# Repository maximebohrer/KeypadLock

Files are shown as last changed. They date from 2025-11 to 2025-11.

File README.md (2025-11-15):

Keypad Door Lock
================

This project turns a conventional door with key into a electronic lock with numerical keypad and password access.

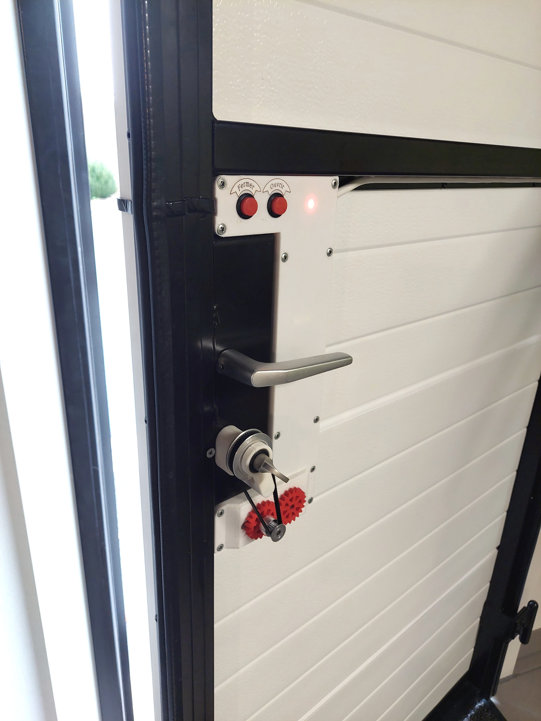
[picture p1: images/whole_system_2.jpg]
Whole system


Most keypad locks that can be bought have all the electronics in the keypad in the exterior of the door, only triggering the door opening by sending a signal to a wire. This means they can be bypassed by dismantling the keypad and touching wires manually.

This version only exposes a passive matrix keypad to the exterior, with all the logic used to interpret the keypresses and opening the door in the inside. There is no way to open the door without knowing the combination, even if the keypad is dismanteled. Two buttons in the inside are used to open or close the door without having to enter the conbination.

Keypad

The system is continuously powered by a 12V supply, which is required for the motor. A LM7805 voltage regulator is used to create 5V for the microcontroller.

The microcontroller used is a Atmel ATmega328P which is the same used in the Adruino Uno and Nano. It is programmed using the Arduino environment.

I needed a motor with the following caracteristics:
- High torque and low speed in a small form factor without the need of a complicated reductor
- Can be rotated by hand when not powered, so that a key can still be used to open the door
- Easily controlled by the microcontroller
The stepper motor is an interesing choice for these reasons, even if we don't necessarily need the precision it offers. It is linked to the key using GT2 pulley and belt with a 3:1 reduction ratio, to get a bit more torque from the motor. The motor is controller by the A4988 IC, to which the microcontroller only has to give step and direction commands.

Motor, pulleys and belt

The system is aware of the position of the key (the rotation angle) with the help of a potentiometer. It is a 10 turn potentiometer (the key has to be able to do multiple full rotations in the door) that is effectively used as a obsolute encoder. It is connected to the key via a 1:1 ratio.

Motor and potentiometer

One LED and buzzer are additionaly used to give feedback to the user.

The PCB was designed on EasyEDA and printed by JLCPCB.

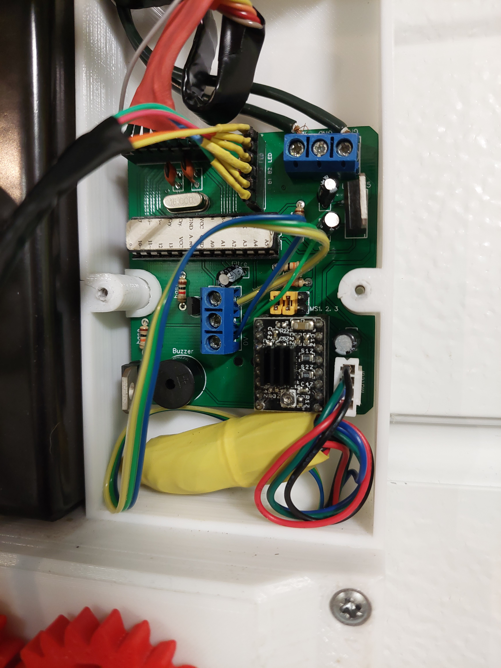
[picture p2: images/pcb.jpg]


The case was designed to fit the door and was 3D-printed. Is has a place for the power supply, PCB, motor and potentiometer, and space for routing cables. It includes a mecanism to tension the GT2 belt by moving the motor+potentiometer block.

Material list
-------------

- ATmega328P with crystal and capacitors
- Nema 17 stepper motor
- A4988 controller
- 12V 5A power supply
- GT2 20-tooth pulley
- GT2 60-tooth pulley
- GT2 280 mm belt
- 8 mm shaft
- 8 mm ball bearing
- 10-turn potentiometer
- 12V 2A power supply
- 12-key keypad
- Red LED
- 2 buttons
- 3D-printed enclosure
- 3D-printed gears
- Custom made PCB
- Wires, screws, etc.

User manual
-----------

```
┌── Log In and Open Door ─────────────────────────────────────────┐
│   ‾‾‾‾‾‾‾‾‾‾‾‾‾‾‾‾‾‾‾‾                                          │
│ You must first unlock the system before you can use any of      │
│ the following commands (except close door)                      │
│  *  0 0 1 2 3 4 5 0 0  #                                        │
│ └┬┘└──────────────┬──┘└─┘                                       │
│  └ start system   └ type the password                           │
│                                                                 │
├── Open Door ───────────────────┬── Close Door ──────────────────┤
│   ‾‾‾‾‾‾‾‾‾                    │   ‾‾‾‾‾‾‾‾‾‾                   │
│ To open the door, use the      │ To close the door, use the     │
│ following command              │ following command              │
│  1  #                          │  0  #                          │
│ └─┘└─┘                         │ └─┘└─┘                         │
│                                │                                │
├── Change Password ─────────────┴────────────────────────────────┤
│   ‾‾‾‾‾‾‾‾‾‾‾‾‾‾‾                                               │
│ To set a new password                                           │
│  7 7 7 1  0 0 1 2 3 4 5 0 0  #                                  │
│ └───────┘└────────┬────────┘└─┘                                 │
│                   └ new password (4 - 12 characters)            │
│                                                                 │
├── Set Trajectory ───────────────────────────────────────────────┤
│   ‾‾‾‾‾‾‾‾‾‾‾‾‾‾                                                │
│ To reset the trajectory and set its first point                 │
│ Move the key to the first position (door fully closed)          │
│ and type the following command                                  │
│  7 7 7 2  #                                                     │
│ └───────┘└─┘                                                    │
│                                                                 │
│ To set the next points (at least 2 in total and up to 10)       │
│ Move the key to the next position and chose the speed at        │
│ which the motor will reach that point                           │
│  7 7 7 2  1 0 0 0  #                                            │
│ └───────┘└───┬───┘└─┘                                           │
│              └ speed to get there in Hz (30 - 10000)            │
│                                                                 │
│ Example with 4 points                                           │
│   7772            77723000          77721000          77723000  │
│     ├─────────────────┼─────────────────┼─────────────────┤     │
│     ↑    ←3000 Hz→    ↑    ←1000 Hz→    ↑    ←3000 Hz→    ↑     │
│ first point     intermediate      intermediate       last point │
│ (door fully         point             point         (door fully │
│   closed)                                              open)    │
│                                                                 │
├── Set Acceleration ─────────────────────────────────────────────┤
│   ‾‾‾‾‾‾‾‾‾‾‾‾‾‾‾‾                                              │
│ To set the rate at which the motor speeds up and slows down     │
│  7 7 7 3  1 0 0 0 0  #                                          │
│ └───────┘└────┬────┘└─┘                                         │
│               └ acceleration in Hz/s (500 - 60000)              │
│                                                                 │
├── Set Timeout ──────────────────────────────────────────────────┤
│   ‾‾‾‾‾‾‾‾‾‾‾                                                   │
│ If the motor can't turn the key and is blocked for this         │
│ amount of time, it will stop and signal the fault               │
│  7 7 7 4  1 0 0 0  #                                            │
│ └───────┘└───┬───┘└─┘                                           │
│              └ timeout value in ms (10 - 5000)                  │
│                                                                 │
├── Installation ─────────────────────────────────────────────────┤
│   ‾‾‾‾‾‾‾‾‾‾‾‾                                                  │
│ The motor must be wired such that it turns in the right         │
│ direction when the OPEN and CLOSE buttons are pressed.          │
│                                                                 │
│ The potentiometer must be wired such that its voltage is at     │
│ its lowest when the door is closed, and increases as the door   │
│ opens.                                                          │
│                                                                 │
└─────────────────────────────────────────────────────────────────┘
```

Programming
-----------

To program microcontrollers in the Arduino envorinment you can use the Arduino IDE, the Arduino extension in VS code, PlatformIO, etc. I used the Arduino IDE.

There are two options to flash a standalone microcontroller:
- The default option: the upload button in the Arduino IDE flashes the program via the serial port (RX and TX pins). This requires a special bootloader on the microcontroller, already preinstalled on Arduino boards, whose job is to listen to the serial port when the microcontroller starts: if something is available, it writes the new program to memory, if not, it justs starts the existing one. [More information](https://docs.arduino.cc/retired/hacking/hardware/building-an-arduino-on-a-breadboard/)
- Flashing using an AVR programmer: it's a chip that directly writes a program to the microcontroller by using its programming pins. To do that we use the "upload via programmer" option of the Arduino IDE. The appropriate programmer has to be chosen in the list. We can even use another Arduino board as a programmer by flashing the ArduinoISP program to it, connecting the correct pins to the microcontroller, and selecting the "Arduino as ISP" programmer in the list. In this case the Arduino bootloader is no longer needed. If we want to use the microcontroller in an Arduino board again, we must use the "burn bootloader" option. [More information](https://docs.arduino.cc/built-in-examples/arduino-isp/ArduinoToBreadboard/)

Electric schematic and PCB
--------------------------

The electric schematic and PCB were created using EasyEDA and printed by JLCPCB.

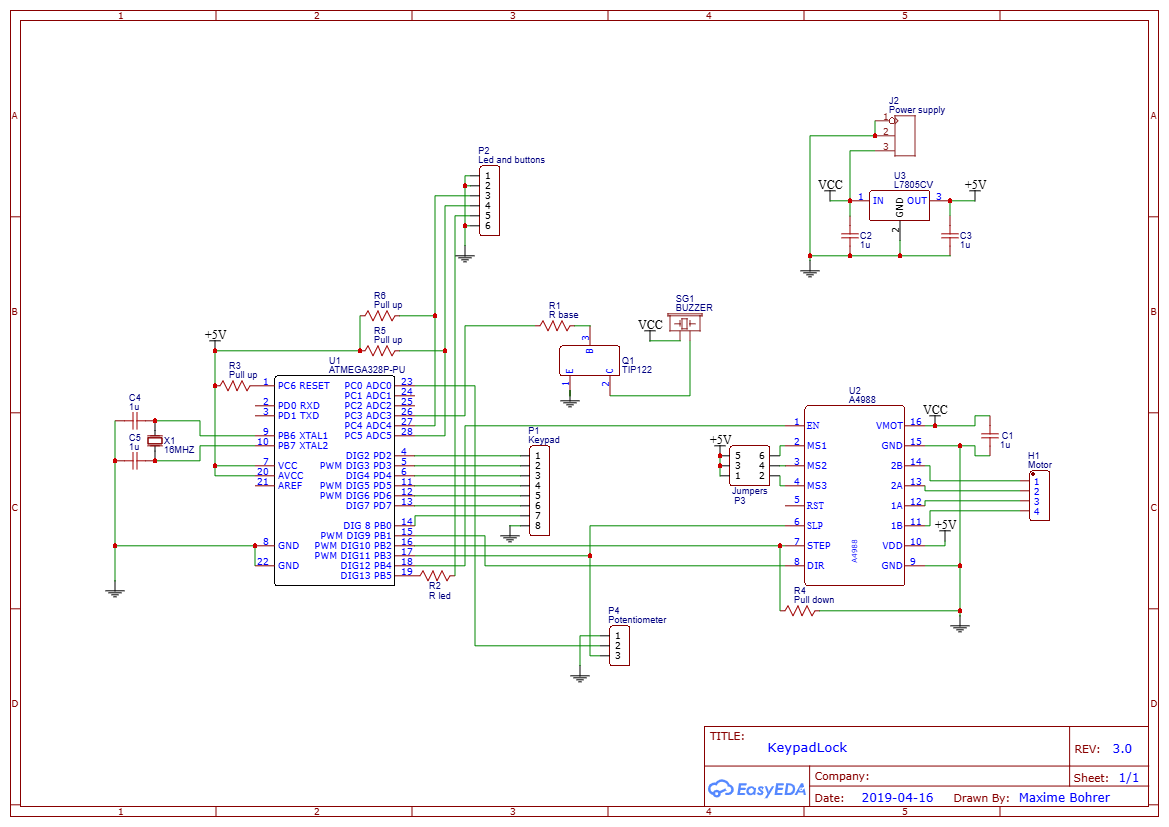
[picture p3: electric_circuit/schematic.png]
Electric schematic

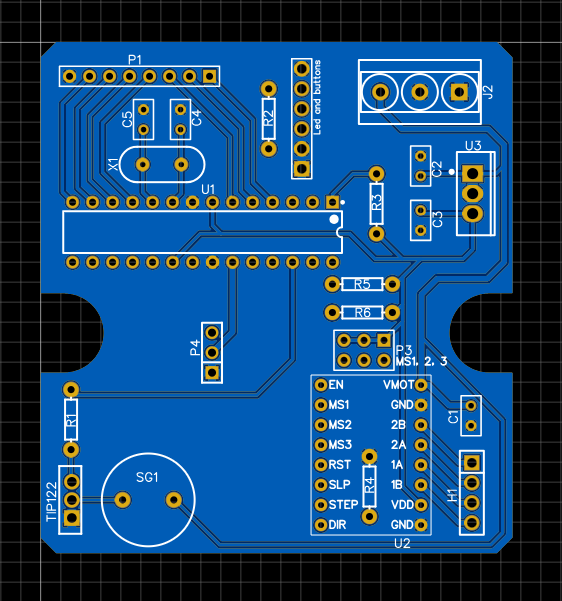
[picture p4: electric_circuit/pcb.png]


3D models
---------

The 3D models were created using Sketchup.

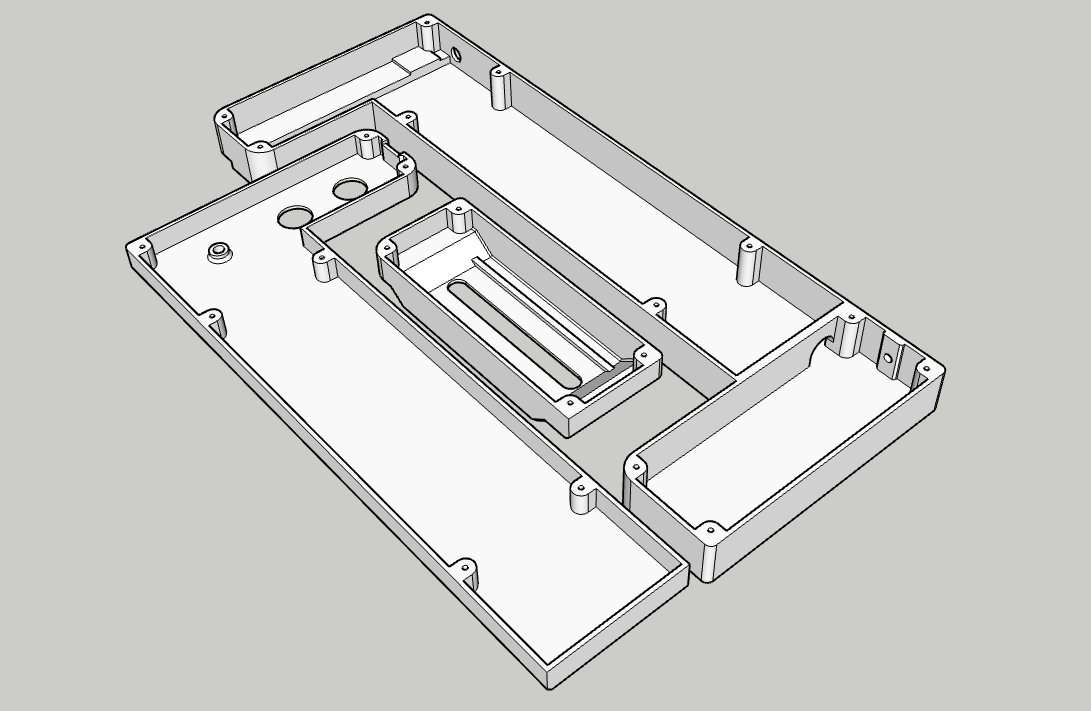
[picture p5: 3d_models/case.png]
Case 3D model


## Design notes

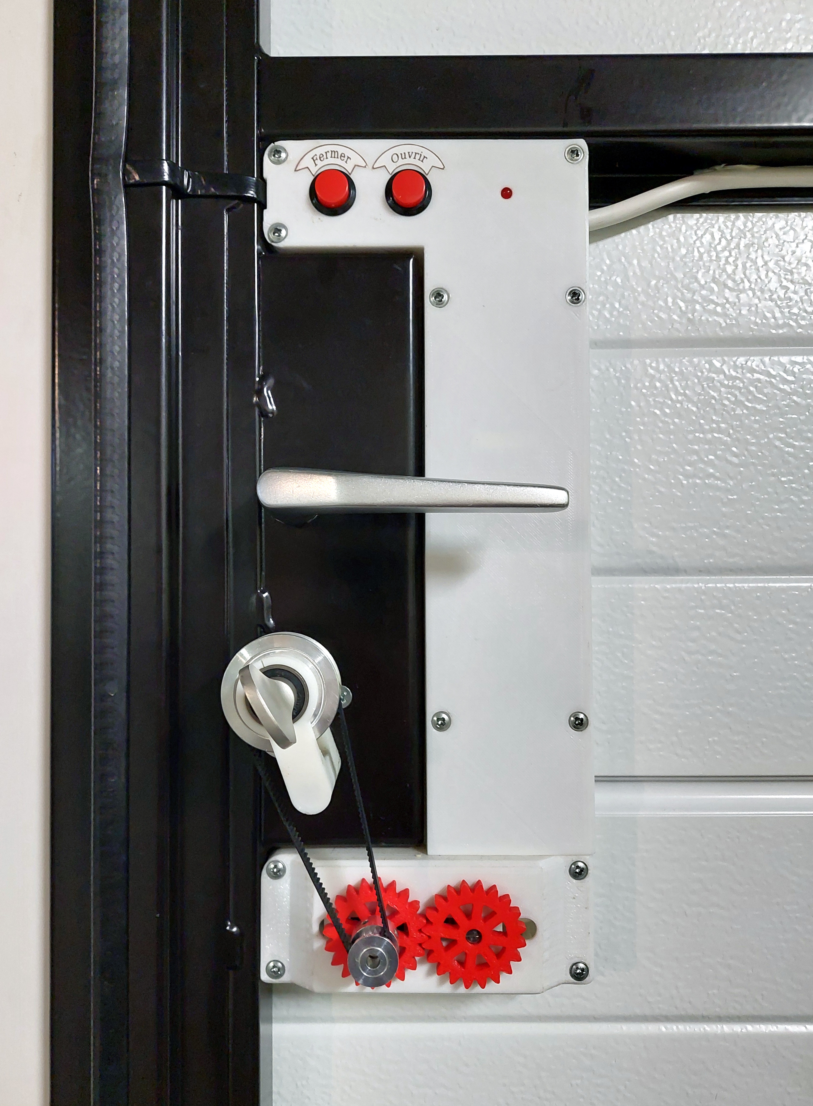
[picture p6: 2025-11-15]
images/whole_system_1.jpg

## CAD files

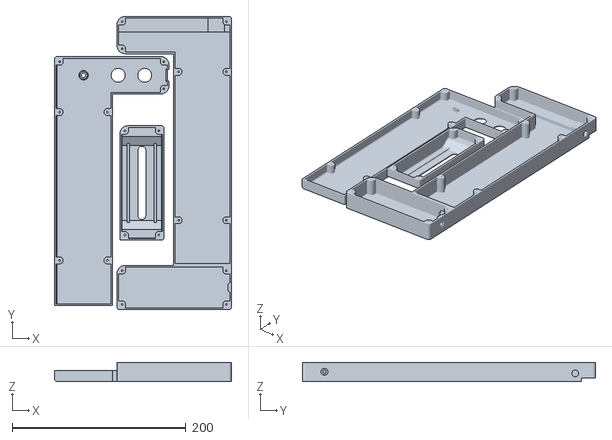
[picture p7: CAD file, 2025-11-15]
3d_models/case.stl
204.0 x 338.0 x 22.1

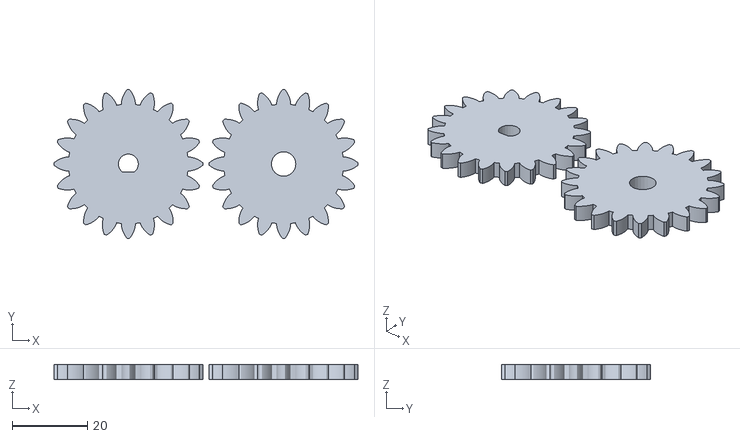
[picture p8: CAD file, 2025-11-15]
3d_models/gears.stl
80.8 x 39.6 x 4.00

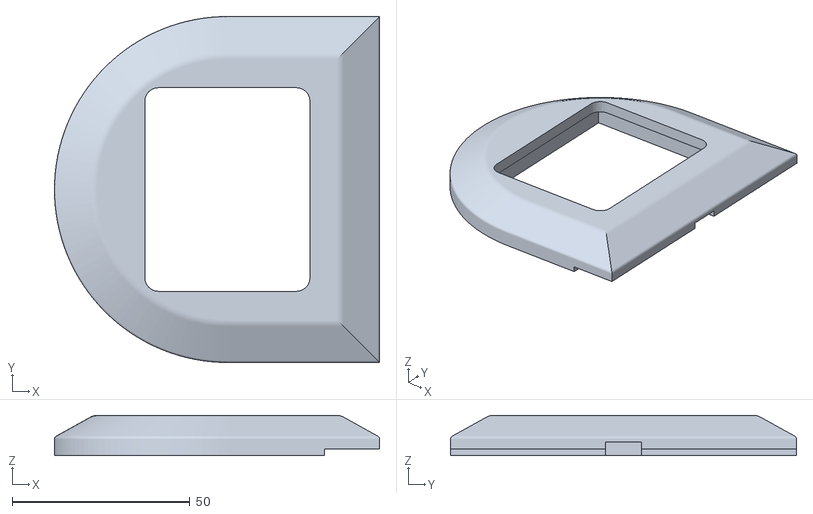
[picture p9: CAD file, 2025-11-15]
3d_models/keypad.stl
91.4 x 97.2 x 11.3

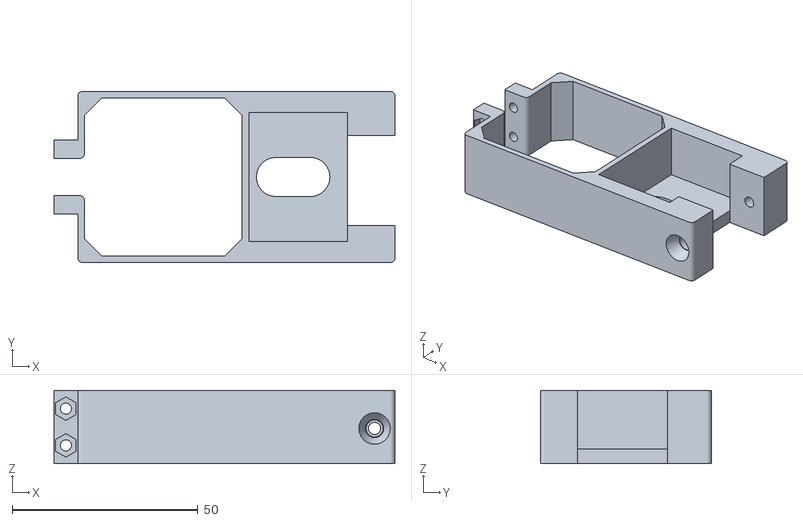
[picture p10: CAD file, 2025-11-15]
3d_models/motor_holder.stl
91.9 x 46.1 x 19.8

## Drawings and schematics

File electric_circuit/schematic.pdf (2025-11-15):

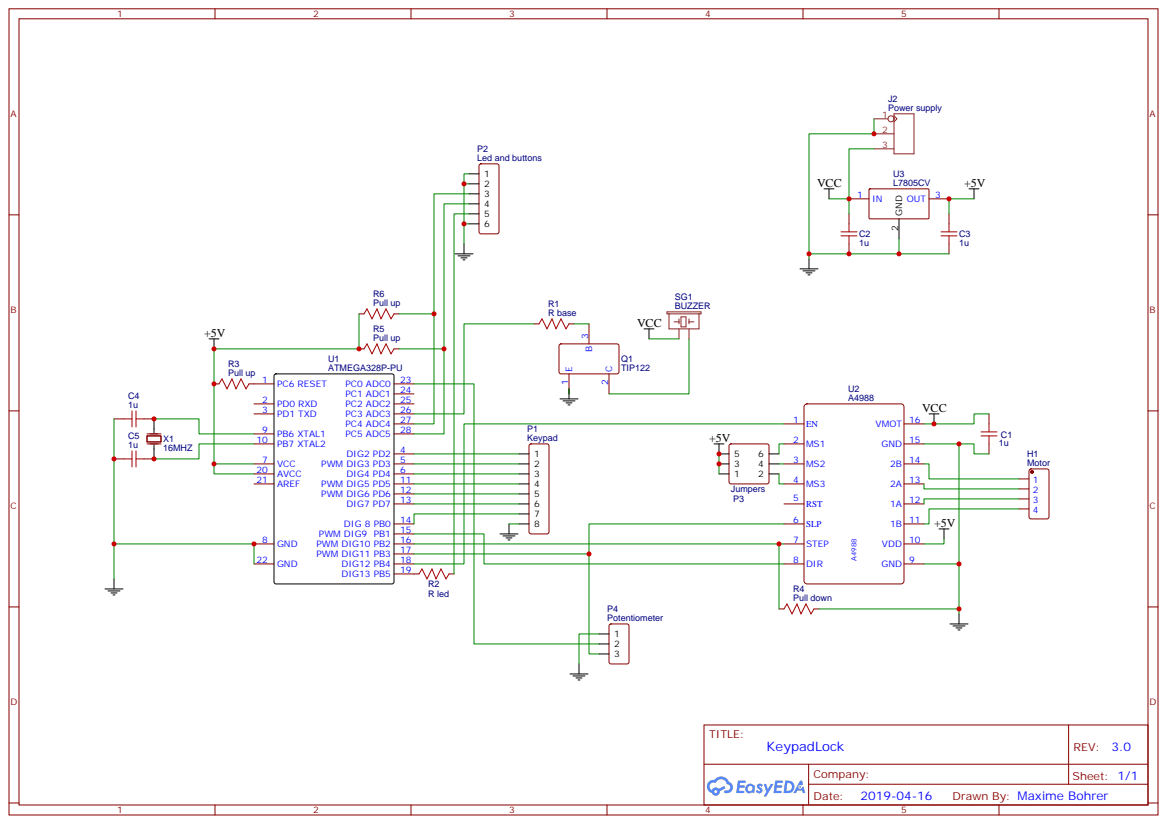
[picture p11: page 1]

Drawn By: Maxime Bohrer

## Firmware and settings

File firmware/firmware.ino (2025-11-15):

#include "SimpleKeypad.h"
#include "SimpleButton.h"
#include "Anim.h"
#include <EEPROM.h>

#define potPin A0       // Potentiometer input pin
#define stepPin 10      // A4988 step signal
#define dirPin 9        // A4988 direction signal
#define enablePin 12    // A4988 enable signal
#define sleepPin 11     // A4988 sleep signal
#define closeBtnPin A4  // Close button
#define openBtnPin A5   // Open button

#define SLEEP 0
#define AWAKE 1
#define UNLOCKED 2

#define TIME_BEFORE_SLEEP 30000

#define MOTOR_STATE_STOP 0
#define MOTOR_STATE_CLOSE 1
#define MOTOR_STATE_OPEN 2
#define MOTOR_STATE_WAIT_CLOSE 3
#define MOTOR_STATE_WAIT_OPEN 4

#define MOTOR_FREQ_ZERO 10
#define MOTOR_FREQ_MIN 30
#define MOTOR_FREQ_MAX 10000
#define MOTOR_FREQ_DEFAULT 1000

#define MOTOR_ACCEL_MIN 500
#define MOTOR_ACCEL_MAX 60000
#define MOTOR_ACCEL_DEFAULT 10000

#define MOTOR_TIMEOUT_MIN 10
#define MOTOR_TIMEOUT_MAX 5000
#define MOTOR_TIMEOUT_DEFAULT 1000

#define INPUT_BUFFER_SIZE 20

// Menu and settings
byte state = SLEEP;
unsigned long sleepTimer = 0;
struct settings {
	char password[INPUT_BUFFER_SIZE];
	int nbStops;
	int stops[10];
	unsigned int speeds[9];
	unsigned int accel;
	int timeout;
};
settings stngs;
bool trajectoryResetted = false;
char input[INPUT_BUFFER_SIZE] = "";
int inputPointer = 0;

// Motor
byte motorState = MOTOR_STATE_STOP;
int depart = 0;
unsigned long motorTimer = 0;
volatile bool stepPinState = 0;
volatile int motorFreq = MOTOR_FREQ_MIN;
volatile int motorFreqTarget = MOTOR_FREQ_MIN;
volatile int remainder = 0;
unsigned long timeoutTimer;
int currentSegment = 0;

// Buttons and keypad
const byte ROWS = 4;
const byte COLS = 3;
char keys[ROWS][COLS] = {
	{'1', '2', '3'},
	{'4', '5', '6'},
	{'7', '8', '9'},
	{'*', '0', '#'}
};
byte rowPins[ROWS] = {3, 8, 7, 5};
byte colPins[COLS] = {4, 2, 6};
SimpleKeypad clav((char*)keys, rowPins, colPins, ROWS, COLS);
SimpleButton closeBtn(closeBtnPin);   // Button on pin A4
SimpleButton openBtn(openBtnPin);     // Button on pin A5
SimpleButton starBtn(rowPins[3]);     // Button '*' of keypad. The star key is both a keypad key and a normal button, so that we can just check for this button in sleep mode instead of scanning the whole keypad.


void setup() {
	pinMode(stepPin, OUTPUT);
	pinMode(dirPin, OUTPUT);
	pinMode(enablePin, OUTPUT);
	pinMode(sleepPin, OUTPUT);
	pinMode(potPin, INPUT);
	pinMode(ledPin, OUTPUT);
	pinMode(buzzerPin, OUTPUT);

	digitalWrite(enablePin, HIGH);
	digitalWrite(sleepPin, LOW);
	digitalWrite(ledPin, HIGH);
	delay(500);
	digitalWrite(ledPin, LOW);
	pinMode(colPins[0], OUTPUT);    // on commance avec la touche * en mode bouton
	digitalWrite(colPins[0], LOW);  //

	// Timer 1 configuration
	TCCR1A = 0b00000000;
	TCCR1B = 0b00001000; // CTC mode (Clear Timer on Compare Match) with OCR1A as top. No clock source (timer stopped).
	TIMSK1 = 0b00000000; // All interrupts are disabled.
	TCNT1 = 0;           // Initializes the timer counter value to 0.

	loadSettings();
	resetCheckOnStartup();
}

void loop() {
	if (state != SLEEP) {
		// System is awake
		char key = clav.getKey();
		if (closeBtn.getState()) {
			// Close button
			if (motorState == MOTOR_STATE_STOP) {
				wakeUp();
				motorStart(MOTOR_STATE_CLOSE);
			} else {
				motorStop();
				beep(ALLUMAGE, false);
			}
		} else if (openBtn.getState()) {
			// Open button
			if (motorState == MOTOR_STATE_STOP) {
				wakeUp();
				motorStart(MOTOR_STATE_OPEN);
			} else {
				motorStop();
				beep(ALLUMAGE, false);
			}
		} else if (key) {
			// Keypad key
			wakeUp();
			if (key == '#') {
				handlePoundKey();
			} else if (key == '*') {
				handleStarKey();
			} else {
				inputAdd(key);
				beep(SHORT_BEEP, false);
			}
		}

		// Calling other loops
		if (motorState != MOTOR_STATE_STOP) {
			motorLoop();   // Motor loop
		} else {
			sleepLoop();   // Sleep management loop
		}
		animLoop();      // Animations loop
	} else {
		// System sleeping
		if (closeBtn.getState()) {
			// Close button
			wakeUp();
			motorStart(MOTOR_STATE_WAIT_CLOSE); // If the system is woken up by the open or close button, give it a bit of time before starting the motor
		} else if (openBtn.getState()) {
			// Open button
			wakeUp();
			motorStart(MOTOR_STATE_WAIT_OPEN);
		} else if (starBtn.getState()) {
			// Star button
			clav.ignoreNextKey('*'); // When the system wakes up, the scan of the keypad will resume, so we need to not register the star key since it's pushed down at this point.
			wakeUp();
			beep(ALLUMAGE, false);
		}
	}
}

void wakeUp() {
	if (state == SLEEP) {
		state = AWAKE;
		ledOn();
		digitalWrite(sleepPin, HIGH);
		digitalWrite(colPins[0], HIGH);
		pinMode(colPins[0], INPUT);
	}
	sleepTimer = millis();
}

void sleep() {
	state = SLEEP;
	digitalWrite(sleepPin, LOW);
	backgroundBlinkOff();
	ledOff();
	noBeep();
	inputReset();
	pinMode(colPins[0], OUTPUT);
	digitalWrite(colPins[0], LOW);
	starBtn.ignoreNextPress();
	trajectoryResetted = false;
}

void sleepLoop() {
	if (millis() - sleepTimer > TIME_BEFORE_SLEEP) {
		sleep();
	}
}

void inputAdd(char c) {
	if (inputPointer < INPUT_BUFFER_SIZE - 1) {
		input[inputPointer] = c;
		inputPointer++;
		input[inputPointer] = '\0'; // Null terminate string
	}
}

void inputReset() {
	inputPointer = 0;
	input[0] = '\0'; // Null terminate string
}

void handleStarKey() {
	if (input[0]) {
		inputReset();
		beep(ALLUMAGE, false);
	} else if (motorState != MOTOR_STATE_STOP) {
		motorStop();
		beep(ALLUMAGE, false);
	} else {
		sleep();
	}
}

void handlePoundKey() {
	if (!strncmp(input, stngs.password, INPUT_BUFFER_SIZE)) {
		state = UNLOCKED;
		motorStart(MOTOR_STATE_OPEN);
	} else if (state == UNLOCKED && !strncmp(input, "1", INPUT_BUFFER_SIZE) && motorState == MOTOR_STATE_STOP) {
		// open
		motorStart(MOTOR_STATE_OPEN);
	} else if (!strncmp(input, "0", INPUT_BUFFER_SIZE) && motorState == MOTOR_STATE_STOP) {
		// close
		motorStart(MOTOR_STATE_CLOSE);
	} else if (state == UNLOCKED && !strncmp(input, "7771", 4)) {
		// Password change
		int len = strnlen(input + 4, INPUT_BUFFER_SIZE - 4);
		if (len >= 4 && len <= 12 && strncmp(input + 4, "777", 3)) {
			strncpy(stngs.password, input + 4, INPUT_BUFFER_SIZE);
			saveSettings();
			beep(VALIDATION, false);
		} else {
			beep(SHORT_ERROR, true);
		}
	} else if (state == UNLOCKED && !strncmp(input, "7772", 4)) {
		// Key rotation trajectory / end stops
		if (!input[4]) {
			// Reset trajectory, save first point (door closed)
			trajectoryResetted = true;
			stngs.stops[0] = get_pos();
			stngs.nbStops = 1;
			saveSettings();
			beep(VALIDATION, false);
		} else {
			// Save next points with associated speeds in Hz (until door open)
			int pos = get_pos();
			long speed = strtol(input + 4, NULL, 10);                 // previous point
			if (trajectoryResetted && stngs.nbStops < 10 && pos > stngs.stops[stngs.nbStops - 1] + 1 && speed >= MOTOR_FREQ_MIN && speed <= MOTOR_FREQ_MAX) {
				stngs.stops[stngs.nbStops] = pos;
				stngs.speeds[stngs.nbStops - 1] = speed;
				stngs.nbStops += 1;
				saveSettings();
				beep(VALIDATION, false);
			} else {
				beep(SHORT_ERROR, true);
			}
		}
	} else if (state == UNLOCKED && !strncmp(input, "7773", 4)) {
		// Acceleration in Hz/s: enables smooth speed transitions during the trajectory
		long accel = strtol(input + 4, NULL, 10);
		if (accel >= MOTOR_ACCEL_MIN && accel <= MOTOR_ACCEL_MAX) {
			stngs.accel = accel;
			saveSettings();
			beep(VALIDATION, false);
		} else {
			beep(SHORT_ERROR, true);
		}
	} else if (state == UNLOCKED && !strncmp(input, "7774", 4)) {
		// Timeout in ms
		long timeout = strtol(input + 4, NULL, 10);
		if (timeout >= MOTOR_TIMEOUT_MIN && timeout <= MOTOR_TIMEOUT_MAX) {
			stngs.timeout = timeout;
			saveSettings();
			beep(VALIDATION, false);
		} else {
			beep(SHORT_ERROR, true);
		}
	} else {
		beep(SHORT_ERROR, true);
	}
	inputReset();
}

void resetCheckOnStartup() {
	int mustReset = 0;
	for (int i = 0; i < 5; i++) {
		delay(20);
		if (!digitalRead(closeBtnPin) && !digitalRead(openBtnPin)) { // 2 buttons pressed at the same time
			mustReset += 1;
		} else {
			break;
		}
	}
	if (mustReset == 5) {
		// Reset every setting to its default value
		strncpy(stngs.password, "001234500", INPUT_BUFFER_SIZE);
		stngs.nbStops = 4;
		stngs.stops[0] = 362; stngs.stops[1] = 462; stngs.stops[2] = 562; stngs.stops[3] = 662;                                     // Example trajectory points
		stngs.speeds[0] = 3 * MOTOR_FREQ_DEFAULT; stngs.speeds[1] = MOTOR_FREQ_DEFAULT; stngs.speeds[2] = 3 * MOTOR_FREQ_DEFAULT;   // Example trajectory speeds
		stngs.accel = MOTOR_ACCEL_DEFAULT;
		stngs.timeout = MOTOR_TIMEOUT_DEFAULT;
		saveSettings();
		tone(buzzerPin, 440, 1000);
		closeBtn.ignoreNextPress();  // do not register button press when the main loop starts
		openBtn.ignoreNextPress();
	}
}

void saveSettings() {
	EEPROM.put(0, stngs);
}

void loadSettings() {
	EEPROM.get(0, stngs);
	if (stngs.nbStops > 10 || stngs.nbStops < 0) stngs.nbStops = 0;
	for (int i = 0; i < stngs.nbStops - 1; i++) {
		if (stngs.speeds[i] < MOTOR_FREQ_MIN || stngs.speeds[i] > MOTOR_FREQ_MAX) {
			stngs.speeds[i] = MOTOR_FREQ_MIN;
		}
	}
	if (stngs.accel < MOTOR_ACCEL_MIN || stngs.accel > MOTOR_ACCEL_MAX) {
		stngs.accel = MOTOR_ACCEL_DEFAULT;
	}
	if (stngs.timeout < MOTOR_TIMEOUT_MIN || stngs.timeout > MOTOR_TIMEOUT_MAX) {
		stngs.timeout = MOTOR_TIMEOUT_DEFAULT;
	}
}

//================================== MOTOR ================================================================================

void motorStart(int direction) {
	// If we need to wait a few ms before starting (to let time to the potentiometer to reach its voltage) we call this function with MOTOR_STATE_WAIT_CLOSE. It will later automatically be called with MOTOR_STATE_CLOSE.
	if (direction == MOTOR_STATE_WAIT_CLOSE || direction == MOTOR_STATE_WAIT_OPEN) {
		motorState = direction;
		motorTimer = millis();
		return;
	}

	// Verify current position, cancel if key already in open or close position
	int pos = get_pos();                                        // first point
	if (stngs.nbStops < 2 || direction == MOTOR_STATE_CLOSE && pos < stngs.stops[0] + 2) {
		motorState = MOTOR_STATE_STOP;
		beep(CLOSE_SUCCESS, true);
		return;                                                   // last point
	} else if (direction == MOTOR_STATE_OPEN && pos > stngs.stops[stngs.nbStops - 1] - 2) {
		motorState = MOTOR_STATE_STOP;
		beep(OPEN_SUCCESS, true);
		return;
	}

	beep(VALIDATION, false);
	motorState = direction; // 1 si ouvrir, 2 si fermer
	backgroundBlinkOn(300);
	digitalWrite(enablePin, LOW);
	stepPinState = 0;
	motorTimer = millis();
	timeoutTimer = millis();
	if (direction == MOTOR_STATE_CLOSE) {
		digitalWrite(dirPin, LOW);
		currentSegment = stngs.nbStops - 2;
		depart = INT16_MAX;
	} else if (direction == MOTOR_STATE_OPEN) {
		digitalWrite(dirPin, HIGH);
		currentSegment = 0;
		depart = INT16_MIN;
	}
	TCCR1A = 0b00000000;
	TCCR1B = 0b00001011;  // CTC mode (Clear Timer on Compare Match) with OCR1A as top. Clock source = prescaler 64 (the timer increments every 64 CPU cycles and resets to 0 when it matches OCR1A.)
	TIMSK1 = 0b00000010;  // Output compare A interrupt enabled.
	TCNT1 = 0;            // Initializes the timer counter value to 0.
	motorFreq = MOTOR_FREQ_ZERO;                     // Current motor frequency (number of motor steps per sec, or number of timer interrupts per sec) (Hz)
	motorFreqTarget = stngs.speeds[currentSegment];  // Motor frequency we want to reach
	OCR1A = 16000000 / 64 / MOTOR_FREQ_ZERO;         // Timer increments 16000000 / 64 = 250000 times per sec. If we set OCR1A to 250000 it will trigger an interrupt every 1 sec. So we divide again by the required frequency.
}

void motorStop() {
	TCCR1A = 0b00000000;
	TCCR1B = 0b00001000;  // CTC mode (Clear Timer on Compare Match) with OCR1A as top. No clock source (timer stopped).
	TIMSK1 = 0b00000000;  // All interrupts are disabled.
	TCNT1 = 0;            // Initializes the timer counter value to 0.
	motorState = MOTOR_STATE_STOP;
	backgroundBlinkOff();
	digitalWrite(dirPin, LOW);
	digitalWrite(enablePin, HIGH);
	wakeUp();
}

ISR(TIMER1_COMPA_vect) { // Interrupt handler comparaison timer1 OCR1A
	stepPinState = !stepPinState;
	digitalWrite(stepPin, stepPinState);

	if (motorFreq < motorFreqTarget) {
		int acceleration = (stngs.accel + remainder) / motorFreq; // The change in frequency according to acceleration is done at every interrupt. We multiply acceleration (Hz/s) by the time sice last interrupt (1 / motorFreq) (s) to find by how many Hz the speed should change.
		remainder = (stngs.accel + remainder) % motorFreq;        // We keep the reminder and add it to the next division, to have less rounding errors, and to prevent the division result from being zero forever.
		motorFreq += acceleration;
		if (motorFreq > motorFreqTarget) motorFreq = motorFreqTarget;
	} else if (motorFreq > motorFreqTarget) {
		int acceleration = (stngs.accel + remainder) / motorFreq;
		remainder = (stngs.accel + remainder) % motorFreq;
		motorFreq -= acceleration;
		if (motorFreq < motorFreqTarget) motorFreq = motorFreqTarget;
	}
	OCR1A = 16000000 / 64 / motorFreq;
}

void motorLoop() {
	if (motorState == MOTOR_STATE_WAIT_CLOSE || motorState == MOTOR_STATE_WAIT_OPEN) {
		if (millis() - motorTimer > 100) {
			motorStart(motorState == MOTOR_STATE_WAIT_OPEN ? MOTOR_STATE_OPEN : MOTOR_STATE_CLOSE);
		}
		return;
	}

	if (millis() - motorTimer > 10) {
		motorTimer = millis();
		int pos = get_pos();

		if (motorState == MOTOR_STATE_CLOSE) {
			// Change speed according to current position and trajectory settings
			if (currentSegment >= 0 && pos < stngs.stops[currentSegment]) {
				currentSegment -= 1;
				motorFreqTarget = currentSegment >= 0 ? stngs.speeds[currentSegment] : MOTOR_FREQ_ZERO;
			}
			// Detection of motor not spinning
			if (pos < depart) {
				depart = pos;
				timeoutTimer = millis();
			}
		} else if (motorState == MOTOR_STATE_OPEN) {
			// Change speed according to current position and trajectory settings
			if (currentSegment < stngs.nbStops - 1 && pos > stngs.stops[currentSegment + 1]) {
				currentSegment += 1;
				motorFreqTarget = currentSegment < stngs.nbStops - 1 ? stngs.speeds[currentSegment] : MOTOR_FREQ_ZERO;
			}
			// Detection of motor not spinning
			if (pos > depart) {
				depart = pos;
				timeoutTimer = millis();
			}
		}

		// Stop motor if not spinning
		if (millis() - timeoutTimer > stngs.timeout) {
			motorStop();
			beep(LONG_ERROR, true);
		}

		// Stop motor when deceleration complete / speed reached zero
		if (motorFreqTarget == MOTOR_FREQ_ZERO && motorFreq == MOTOR_FREQ_ZERO) {
			int lastState = motorState;
			motorStop();
			beep(lastState == MOTOR_STATE_OPEN ? OPEN_SUCCESS : CLOSE_SUCCESS, false);
		}
	}
}

int get_pos() {
	return analogRead(potPin);
}

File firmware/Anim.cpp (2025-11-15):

#include "Anim.h"

int ALLUMAGE[] = {440, 50, 659, 50, -1};
int VALIDATION[] = {554, 50, 659, 50, 880, 100, -1};
int SHORT_BEEP[] = {659, 100, -1};
int SHORT_ERROR[] = {200, 100, 0, 50, 200, 100, -1};
int LONG_ERROR[] = {200, 100, 0, 50, 200, 100, 0, 50, 200, 1000, -1};
int OPEN_SUCCESS[] = {440, 50, 554, 50, 659, 50, 880, 50, 1108, 50, 1319, 50, 1760, 100, -1};
int CLOSE_SUCCESS[] = {1760, 50, 1319, 50, 1108, 50, 880, 50, 659, 50, 554, 50, 440, 100, -1};

bool currentLedState = false;

bool defaultLedState = false;  // Priority 0

int backgroundBlink = 0;       // Priority 1
unsigned long blinkTimer = 0;

int *sound = NULL;             // Priority 2
bool errorBlink = false;
unsigned long beepTimer = 0;


void ledOn() {
	defaultLedState = true;
	if (!backgroundBlink && !sound) {
		currentLedState = true;
		digitalWrite(ledPin, true);
	}
}

void ledOff() {
	defaultLedState = false;
	if (!backgroundBlink && !sound) {
		currentLedState = false;
		digitalWrite(ledPin, false);
	}
}

void backgroundBlinkOn(int freq) {
	backgroundBlink = freq;
	if (!sound) {
		blinkStart();
	}
}

void backgroundBlinkOff() {
	backgroundBlink = 0;
	if (!sound) {
		currentLedState = defaultLedState;
		digitalWrite(ledPin, defaultLedState);
	}
}

void blinkStart() {
	currentLedState = !currentLedState;
	digitalWrite(ledPin, currentLedState);
	blinkTimer = millis();
}

void animLoop() {
	if (sound) {
		if (millis() - beepTimer > *(sound+1)) {
			sound += 2;
			if (*sound > -1) {
				beepTimer = millis();
				if (*sound) tone(buzzerPin, *sound, *(sound+2) > 0 ? 2000 : *(sound+1));
			} else {
				noBeep();
			}
		}
		if (errorBlink) {
			if (millis() - blinkTimer > 50) {
				blinkTimer = millis();
				currentLedState = !currentLedState;
				digitalWrite(ledPin, currentLedState);
			}
		}
	} else if (backgroundBlink) {
		if (millis() - blinkTimer > backgroundBlink) {
			blinkTimer = millis();
			currentLedState = !currentLedState;
			digitalWrite(ledPin, currentLedState);
		}
	}
}

void beep(int *song, bool error) {
	errorBlink = error;
	sound = song;
	beepTimer = millis();
	if (*sound) tone(buzzerPin, *sound, *(sound+2) > 0 ? 2000 : *(sound+1));
	if (!error) {
		currentLedState = false;
		digitalWrite(ledPin, false);
	} else {
		blinkStart();
	}
}

void noBeep() {
	noTone(buzzerPin);
	sound = NULL;
	errorBlink = false;
	if (backgroundBlink) {
		blinkStart();
	} else {
		currentLedState = defaultLedState;
		digitalWrite(ledPin, defaultLedState);
	}
}
